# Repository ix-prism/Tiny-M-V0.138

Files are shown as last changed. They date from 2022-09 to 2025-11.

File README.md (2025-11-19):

# Tiny-M + Voron0.2 Mod
a mod for Voron0/Tiny-M 3D printer/一个基于Voron0/Tiny-M的3D打印机mod

This project is based on Tiny-M by Guido (gsl12).
Thanks for the great idea and all the work he put into it.

# 与 Tiny-M 的区别 / Differences from Tiny-M

- Voron 0.2 风格化外观  
  Stylized in the style of Voron 0.2

- 使用 MiniFrontBurner 打印头，支持 E3D V6 或 Bambu 热端  
  Uses the MiniFrontBurner toolhead, compatible with E3D V6 or Bambu hotends

- X 轴导轨更换为侧面安装的 MGN9H  
  X-axis linear rail replaced with a side-mounted MGN9H

- 挤出机更换为 Sherpa Mini  
  Extruder changed to Sherpa Mini

- 屏幕更换为 V0Display  
  Display replaced with V0Display

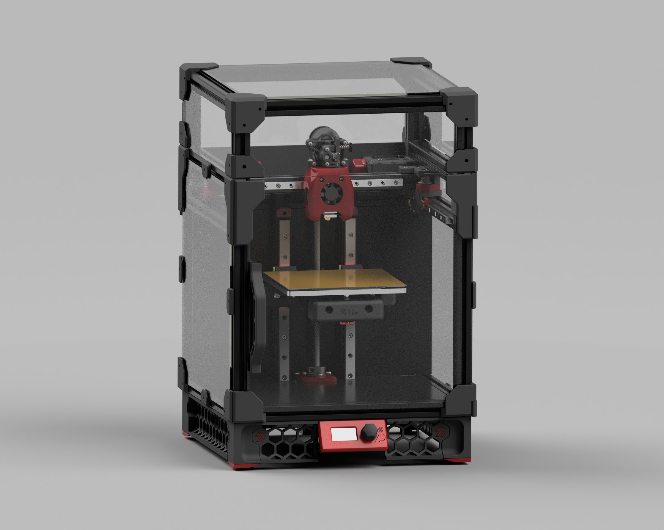
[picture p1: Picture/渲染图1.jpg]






)

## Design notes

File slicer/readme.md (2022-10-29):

切片配置文件建议套用Voron0.1或2.4的预设，并将平台大小改为150x150，高度150。

并更改打印机设置中的：

起始Gcode:

PrusaSlicer:

; M190 S0
; M109 S0 ; uncomment to remove set&wait temp gcode added automatically after this start gcode
print_start HOTEND=[first_layer_temperature[initial_tool]] BED=[first_layer_bed_temperature]

cura:

PRINT_START BED={material_bed_temperature_layer_0} HOTEND={material_print_temperature_layer_0}

SuperSlicer:

; M190 S0
; M109 S0 ; uncomment to remove set&wait temp gcode added automatically after this start gcode
print_start HOTEND={first_layer_temperature[initial_extruder] + extruder_temperature_offset[initial_extruder]} BED=[first_layer_bed_temperature] CHAMBER=[chamber_temperature]

结束Gcode:

print_end

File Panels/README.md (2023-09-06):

## Voron0.2样式封箱

### 黑色

Deck_Panel x1

Back_Panel x1

### 透明
门板 
270x294mm x1

侧板 
270x278mm x2

顶罩 
270x270mm x1

270x80mm  x5

厚度3mm

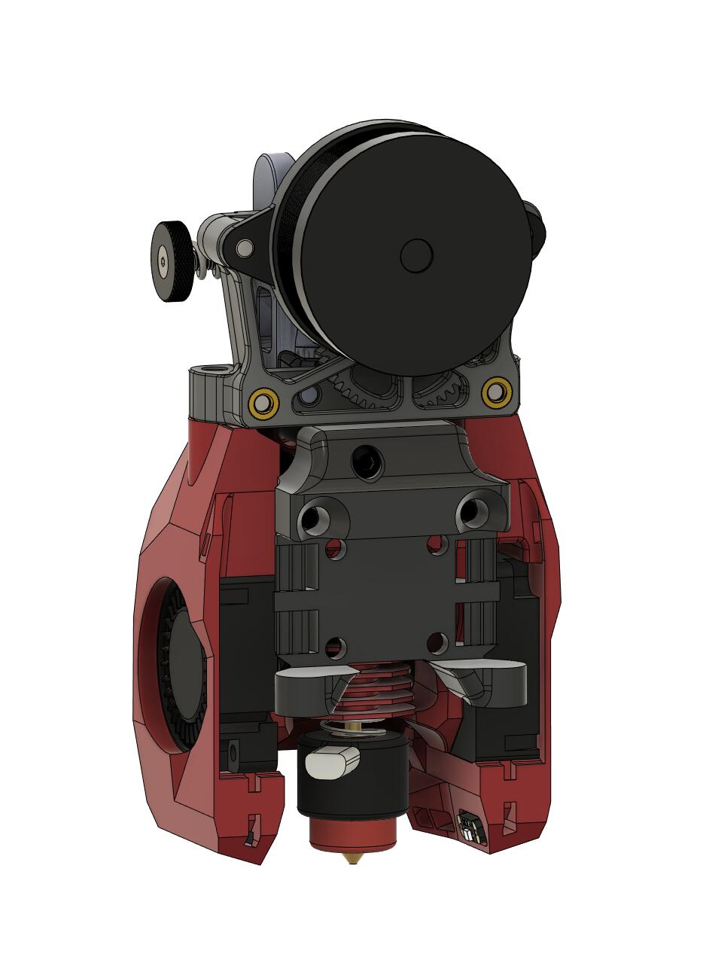
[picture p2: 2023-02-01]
Picture/Mini Stealthburner-Sherpa2.jpg

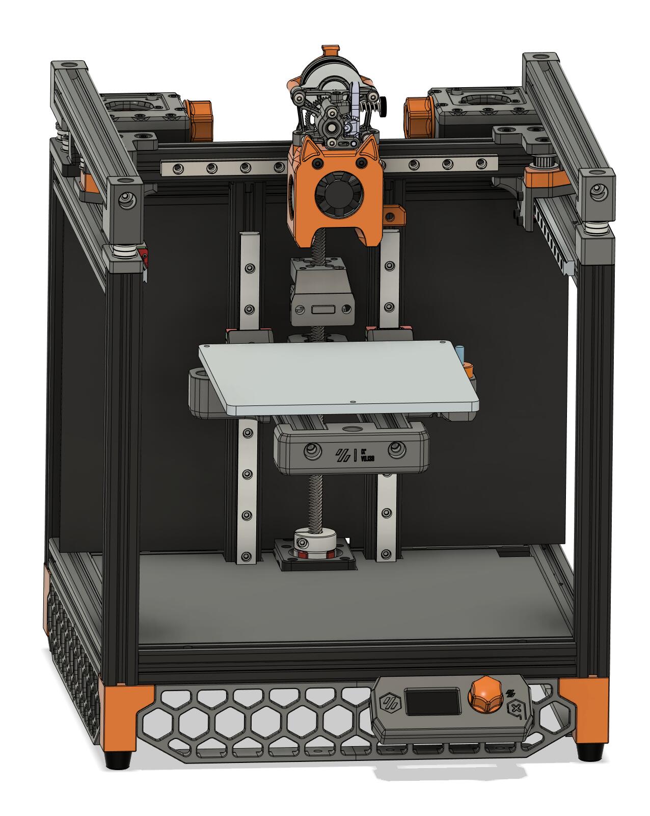
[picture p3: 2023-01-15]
Picture/rc2.jpg

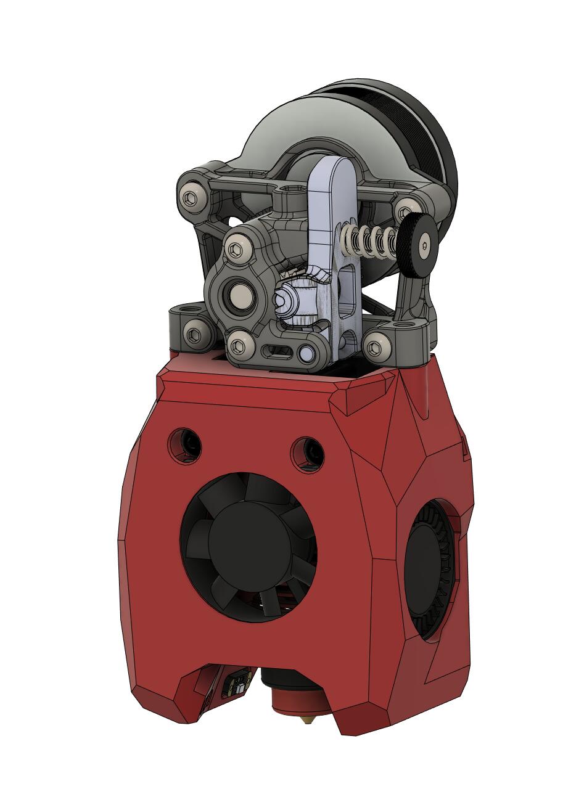
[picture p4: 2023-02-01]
Picture/Mini Stealthburner-Sherpa1.jpg

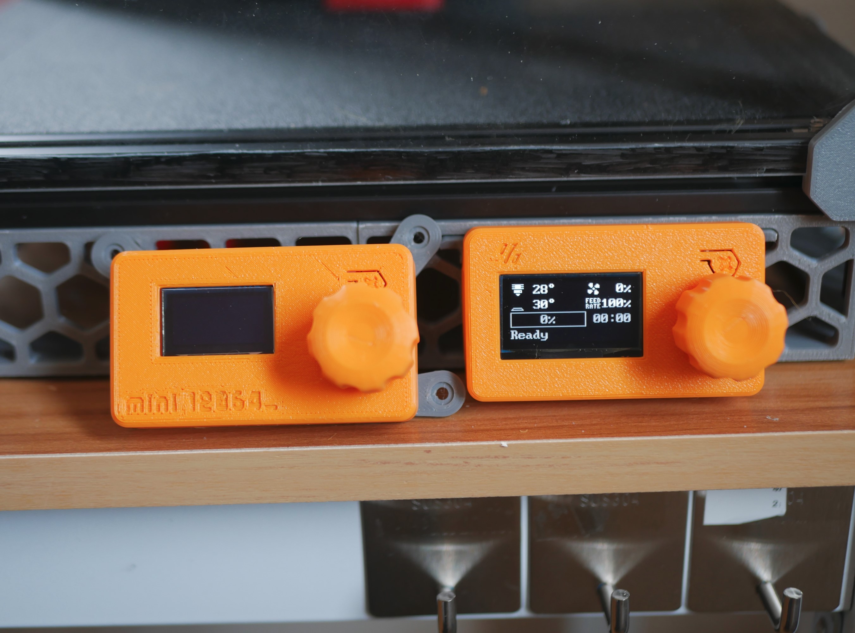
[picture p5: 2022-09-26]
Picture/实拍图1.jpg

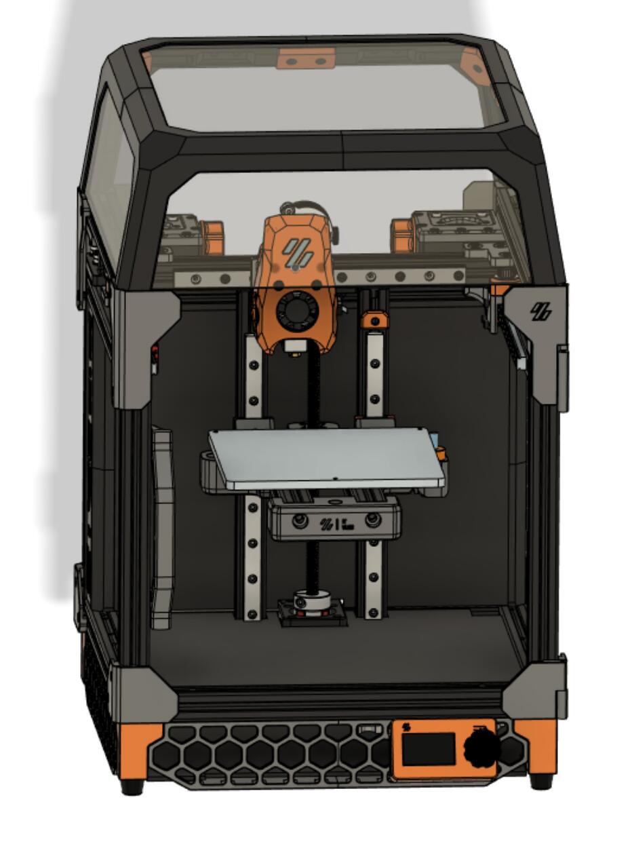
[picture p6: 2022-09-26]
Picture/picture.jpg

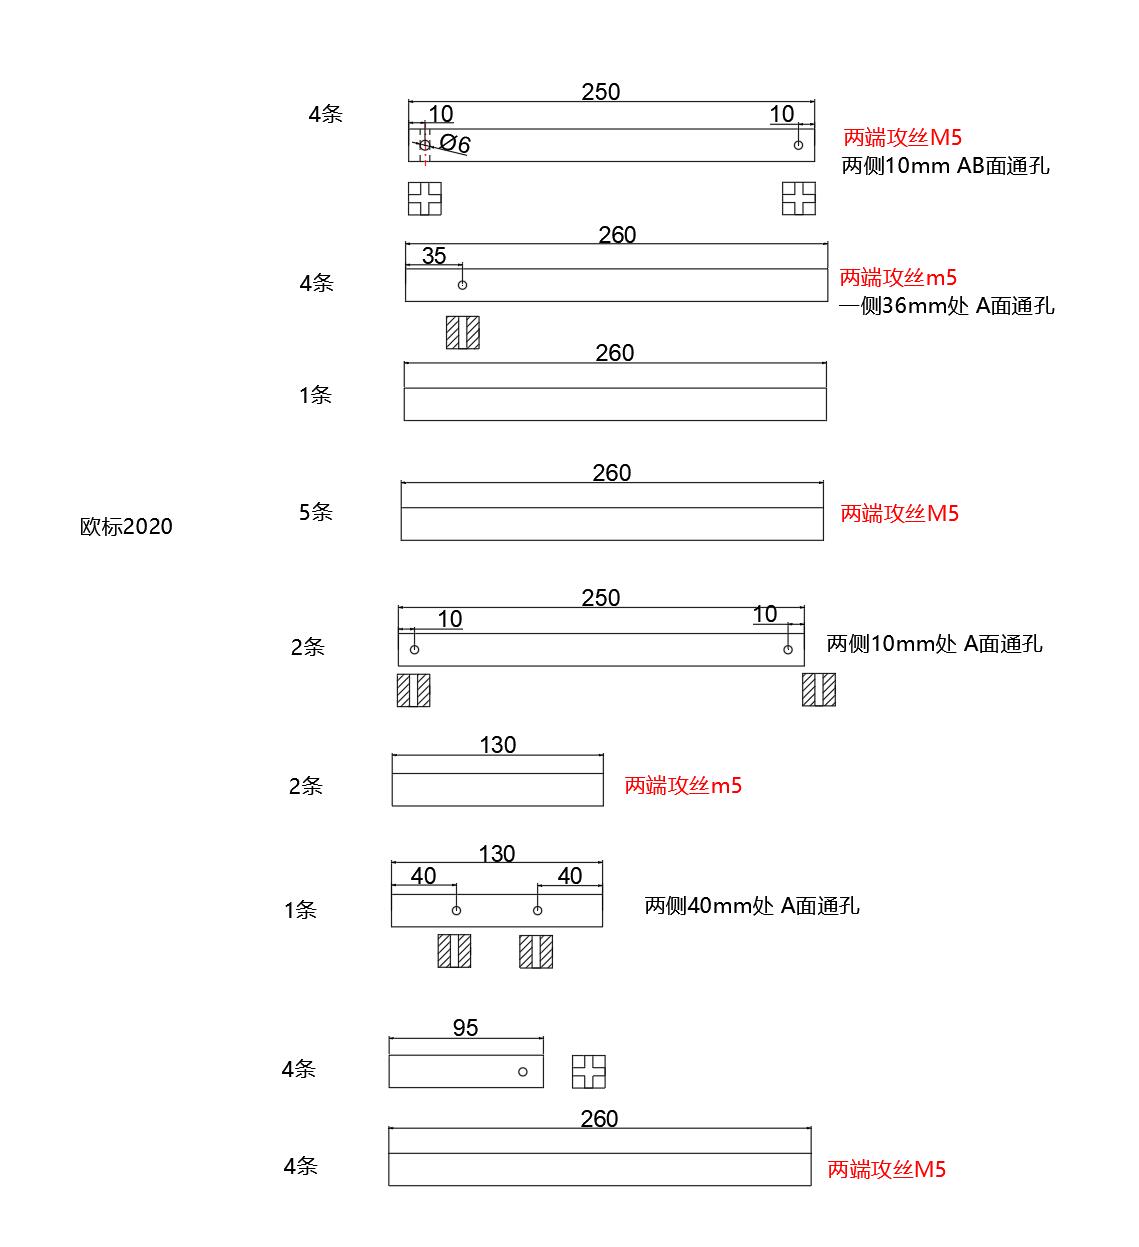
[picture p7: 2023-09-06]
frame/FRAME.jpg

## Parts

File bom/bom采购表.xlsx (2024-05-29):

 | 型号 | 数量 | 参考
紧固件 | m3x8 杯头 | 60 | https://detail.tmall.com/item.htm?abbucket=9&id=18273546578&ns=1&priceTId=213e391a17169841317497723e8a6d
 | m3x10 杯头 | 60 | https://detail.tmall.com/item.htm?abbucket=9&id=18273546578&ns=1&priceTId=213e391a17169841317497723e8a6d
 | m3x12 杯头 | 20 | https://detail.tmall.com/item.htm?abbucket=9&id=18273546578&ns=1&priceTId=213e391a17169841317497723e8a6d
 | m3x16 杯头 | 2 | https://detail.tmall.com/item.htm?abbucket=9&id=18273546578&ns=1&priceTId=213e391a17169841317497723e8a6d
 | m3x20 杯头 | 10 | https://detail.tmall.com/item.htm?abbucket=9&id=18273546578&ns=1&priceTId=213e391a17169841317497723e8a6d
 | m3x25 杯头 | 10 | https://detail.tmall.com/item.htm?abbucket=9&id=18273546578&ns=1&priceTId=213e391a17169841317497723e8a6d
 | m3x30 杯头 | 10 | https://detail.tmall.com/item.htm?abbucket=9&id=18273546578&ns=1&priceTId=213e391a17169841317497723e8a6d
 | m3x35 杯头 | 20 | https://detail.tmall.com/item.htm?abbucket=9&id=18273546578&ns=1&priceTId=213e391a17169841317497723e8a6d
 | m3x40 杯头 | 2 | https://detail.tmall.com/item.htm?abbucket=9&id=18273546578&ns=1&priceTId=213e391a17169841317497723e8a6d
 | m3x45 杯头 | 3 | https://detail.tmall.com/item.htm?abbucket=9&id=18273546578&ns=1&priceTId=213e391a17169841317497723e8a6d
 | m2x10自攻 | 20 | https://detail.tmall.com/item.htm?id=26788024998&rn=32485e43cd554b61808184f56eb92091&abbucket=6
 | m4x10杯头 | 4 | https://detail.tmall.com/item.htm?abbucket=9&id=18273546578&ns=1&priceTId=213e391a17169841317497723e8a6d
 | m5x8圆头 | 30 | https://detail.tmall.com/item.htm?id=35703239201&rn=ca5bd9221a8a0a63bc05ffa24d3150ff&abbucket=6
 | m5x10圆头 | 30 | https://detail.tmall.com/item.htm?id=35703239201&rn=ca5bd9221a8a0a63bc05ffa24d3150ff&abbucket=6
 | m5x16圆头 | 25 | https://detail.tmall.com/item.htm?id=35703239201&rn=ca5bd9221a8a0a63bc05ffa24d3150ff&abbucket=6
 | m5x30圆头 | 4 | https://detail.tmall.com/item.htm?id=35703239201&rn=ca5bd9221a8a0a63bc05ffa24d3150ff&abbucket=6
 | m5x35圆头 | 4 | https://detail.tmall.com/item.htm?id=35703239201&rn=ca5bd9221a8a0a63bc05ffa24d3150ff&abbucket=6
 | M5x40杯头 | 4 | https://detail.tmall.com/item.htm?abbucket=9&id=18273546578&ns=1&priceTId=213e391a17169841317497723e8a6d
 | M5x55圆头 | 4 | https://detail.tmall.com/item.htm?id=35703239201&rn=ca5bd9221a8a0a63bc05ffa24d3150ff&abbucket=6
 | 20型 M3弹珠螺母 | 30 | https://detail.tmall.com/item.htm?id=602648155862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
 | 20型 M5弹珠螺母 | 30 | https://detail.tmall.com/item.htm?id=602648155862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
 | M3六角螺母 | 4 | https://detail.tmall.com/item.htm?id=20955552239&rn=f7722f9d702b8c245503003701b63420&abbucket=6
 | M3 T螺母 | 70 | https://detail.tmall.com/item.htm?id=602648155862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
 | M5 T螺母 | 30 | https://detail.tmall.com/item.htm?id=602648155862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
 | 3x4x5土八热熔螺母 | 30 | https://detail.tmall.com/item.htm?priceTId=2147bfe017169844482451716efa16&id=654516657514&ns=1&abbucket=9
 | 5x6x7土八热熔螺母 |  | https://detail.tmall.com/item.htm?priceTId=2147bfe017169844482451716efa16&id=654516657514&ns=1&abbucket=9
 | 1x8x25黄色模具弹簧 | 3 | https://item.taobao.com/item.htm?priceTId=215040fc17169846375948829efd79&id=16269938500&ns=1&abbucket=9
传动件 | F695ZZ轴承 | 20 | https://item.taobao.com/item.htm?priceTId=215040fc17169846551052507efd79&id=650278182280&ns=1&abbucket=9
 | 5x8x1间隙垫片 | 20 | https://item.taobao.com/item.htm?priceTId=215040fc17169846849985018efd79&id=610328378642&ns=1&abbucket=9
 | T8丝杆导程8 210mm | 1 | https://item.taobao.com/item.htm?priceTId=215040fc17169847291951068efd79&id=559693268692&ns=1&abbucket=9
 | 联轴器 5x8mm | 1 | https://item.taobao.com/item.htm?priceTId=215040fc17169847469882688efd79&id=584297719001&ns=1&abbucket=9
 | 42步进电机（XY） |  | https://item.taobao.com/item.htm?priceTId=215040fc17169847953456946efd79&id=670665930208&ns=1&abbucket=9
 | 42步进电机（Z） | 3 | https://item.taobao.com/item.htm?priceTId=215040fc17169847607943979efd79&id=649664531631&ns=1&abbucket=9
 | 2GT同步轮 20齿 内孔5 | 3 | https://item.taobao.com/item.htm?priceTId=2147828b17169848125175875e9536&id=577469956078&ns=1&abbucket=9
 | 2GT惰轮20齿 内孔5 | 2 | https://item.taobao.com/item.htm?priceTId=2147828b17169848125175875e9536&id=559682437946&ns=1&abbucket=9
 | 35mm圆柱销 切槽（Voron2.4限位同款） | 1 | https://item.taobao.com/item.htm?priceTId=2147828b17169848327376922e9536&id=681231933442&ns=1&abbucket=9
 | mgn9h直线导轨 200mm | 3 | https://detail.tmall.com/item.htm?id=617754103685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
 | mgn12h直线导轨 200mm | 2
 | 2GT 6mm皮带 | 3 | https://item.taobao.com/item.htm?priceTId=2147828b17169848770261321e9536&id=719632885878&ns=1&abbucket=9
电子元件 | 微动开关 d2f 带弹片x2 不带弹片x1 | 3 | https://item.taobao.com/item.htm?priceTId=2147828b17169849159123369e9536&id=18868641543&ns=1&abbucket=9
 | 香橙派Zero 3 | 1 | https://detail.tmall.com/item.htm?priceTId=2147828b17169849839767753e9536&id=728078846964&ns=1&abbucket=9
 | 32GB TF卡 读卡器 | 1 | https://detail.tmall.com/item.htm?priceTId=2147828b17169849647936550e9536&id=659968673994&ns=1&abbucket=9
 | Bigtreetech SKR PICO | 1 | https://item.taobao.com/item.htm?priceTId=2147828b17169849432475100e9536&id=668879699263&ns=1&abbucket=9
 | 200W 24V开关电源 | 1 | https://detail.tmall.com/item.htm?id=546975228335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
 | C14电源插座 | 1 | https://item.taobao.com/item.htm?priceTId=2147822f17169850475763810efc68&id=652256774750&ns=1&abbucket=9
 | C13电源线 | 1 | https://item.taobao.com/item.htm?priceTId=2147820f17169850937438831e0b78&id=743432903716&ns=1&abbucket=9
 | 3010鼓风机 24V 15000rpm | 2 | https://item.taobao.com/item.htm?priceTId=2147820f17169851137411955e0b78&id=674712023015&ns=1&abbucket=9
 | 3010轴流风扇 24V 11000rpm | 1 | https://item.taobao.com/item.htm?spm=a1z10.3-c.w4002-22813209058.13.62e347bbOxIzJz&id=677180233734
 | V0Display OLED屏 | 1 | https://item.taobao.com/item.htm?priceTId=2147822717169851415963970e05de&id=710412503507&ns=1&abbucket=9
 | 18awg导线 | 1
 | 型号 | 数量
 | 风扇延长线 | 1
挤出机 | 拓竹热端 | 1 | https://item.taobao.com/item.htm?priceTId=2147822717169851780266019e05de&id=730602674552&ns=1&abbucket=9
 | 36圆饼步进电机 | 1 | https://item.taobao.com/item.htm?priceTId=2147822717169851924886664e05de&id=701941466920&ns=1&abbucket=9
 | BMG挤出机齿轮套件 | 1 | https://item.taobao.com/item.htm?spm=a1z10.3-c.w4002-24486160586.11.f24340daE31Nld&id=731773857096
 | 3x4mm铁氟龙管 | 1 | https://detail.tmall.com/item.htm?priceTId=2147826717169852219491882e4ea2&id=520837614528&ns=1&abbucket=9
 | 2x4mm铁氟龙管 | 1 | https://detail.tmall.com/item.htm?priceTId=2147826717169852219491882e4ea2&id=520837614528&ns=1&abbucket=9
杂项 | 橡胶脚垫 内孔5 | 4 | https://item.taobao.com/item.htm?priceTId=214781b217169852806426253eefb3&id=678365614319&ns=1&abbucket=9
 | 10X11 R18可开拖链 | 1 | https://item.taobao.com/item.htm?priceTId=214781b217169852939376897eefb3&id=676337595083&ns=1&abbucket=9
 | 尼龙理线网 | 1 | https://item.taobao.com/item.htm?priceTId=214782b617169853084064094edc52&id=23733868415&ns=1&abbucket=9
 | 尼龙扎带 | 10
 | 亚克力板 | 2
 | 理线槽15cm | 1 | https://click.simba.taobao.com/cc_im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
 | 3M双面胶 | 1
铝型材 | 250mm 两侧10mm通孔 攻丝 | 4
 | （四根立柱）
 | 260mm 一侧36mm通孔 攻丝 | 4
 | （Y左右线轨固定，线轨下方横梁）
 | 260mm 无其他处理 | 1
 | （X轴线轨）
 | 260mm 两端攻丝 | 5
 | （横梁）
 | 250mm 两端10mm通孔 | 2
 | （Z轴线轨）
 | 130mm 两端攻丝 | 1
 | （热床）
 | 130mm 两侧40mm通孔 | 2
 | （热床）
热床 | 150x150x6超平铝板 | 1
 | 120W 100x100加热垫 | 1
 | 150x150 PEI喷涂磁吸平台 | 1

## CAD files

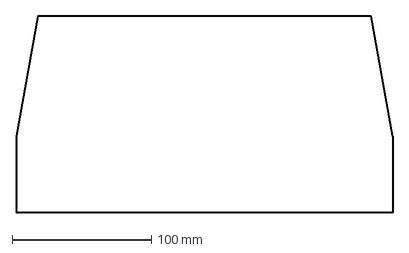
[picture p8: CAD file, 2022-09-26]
Panels/【透明】顶罩后.dxf
270.4 x 141.5 mm

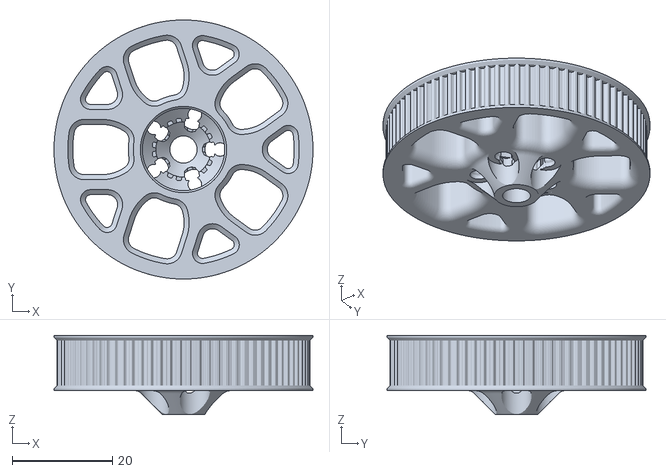
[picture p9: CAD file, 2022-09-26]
stls/Bed/belt_z/皮带z_80T.stl
51.6 x 51.6 x 15.8

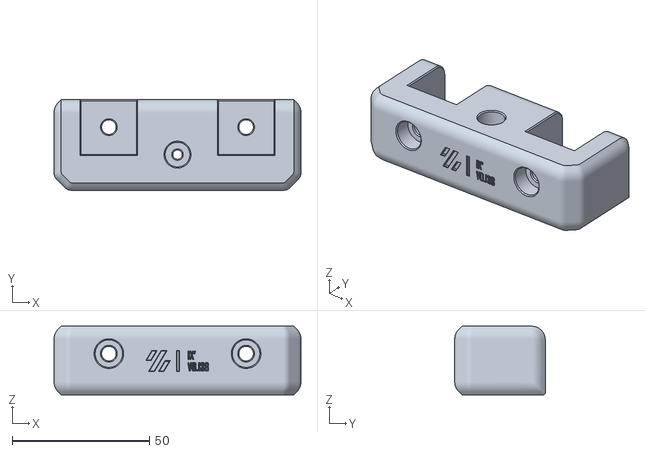
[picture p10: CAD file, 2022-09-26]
stls/Bed/带logo.stl
90.0 x 33.0 x 25.0

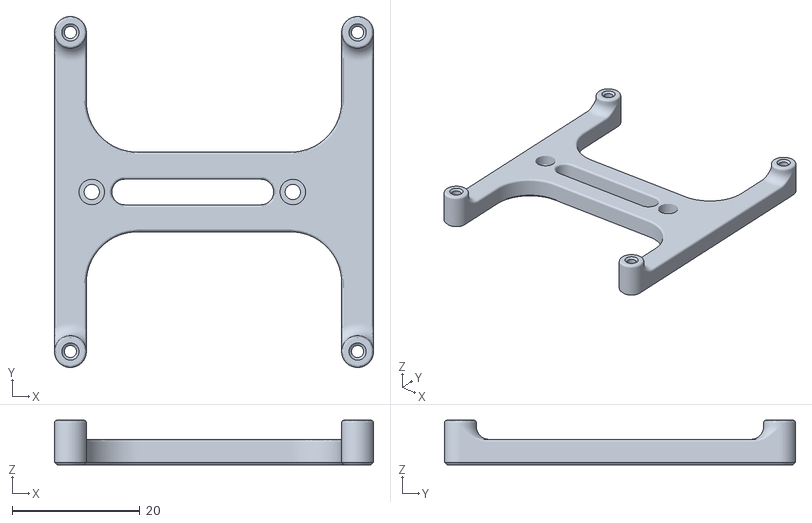
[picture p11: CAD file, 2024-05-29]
stls/Electronics/orangepi zero3 bracket.stl
50.0 x 55.0 x 7.00

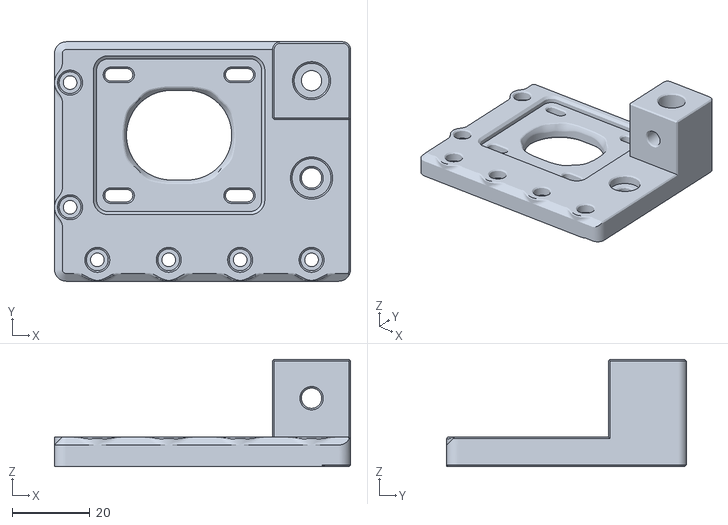
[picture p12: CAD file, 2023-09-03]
stls/Gantry/AB_drive_units/ab_drive v4 - b_drive_right_top_V4_V1.stl
76.0 x 61.5 x 27.6

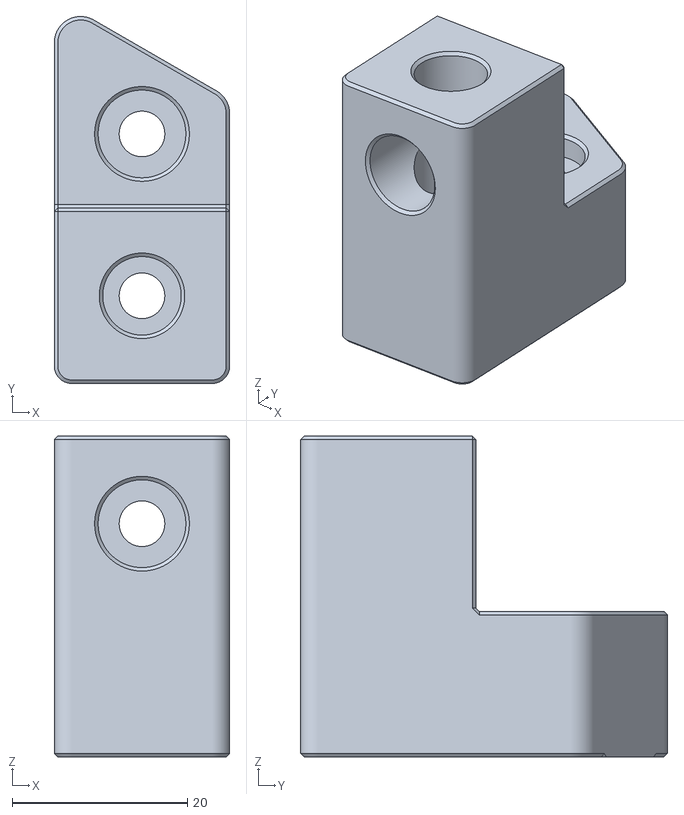
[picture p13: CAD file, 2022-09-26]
stls/Gantry/Front-Idler/front_idler_left_top_V4.stl
20.0 x 41.9 x 36.6

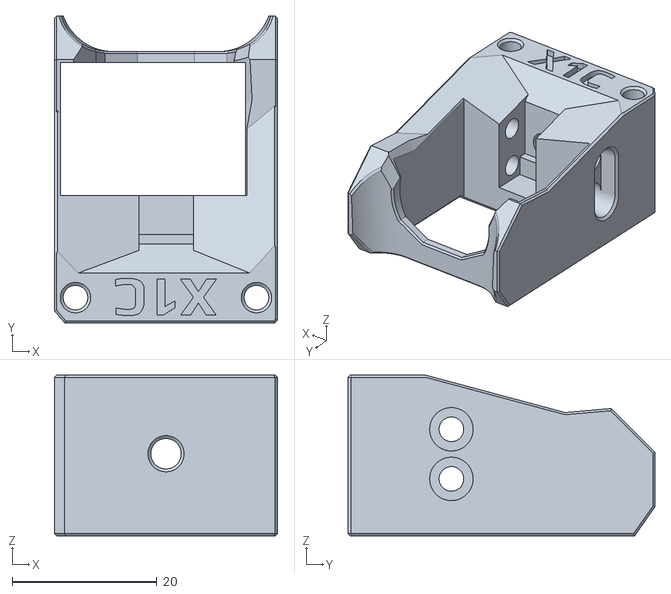
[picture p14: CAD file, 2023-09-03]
stls/Gantry/X_Axis/X_Carriage/[a]_FS_Hotend_Mount_Bambu_X1C.stl
30.8 x 42.4 x 22.2

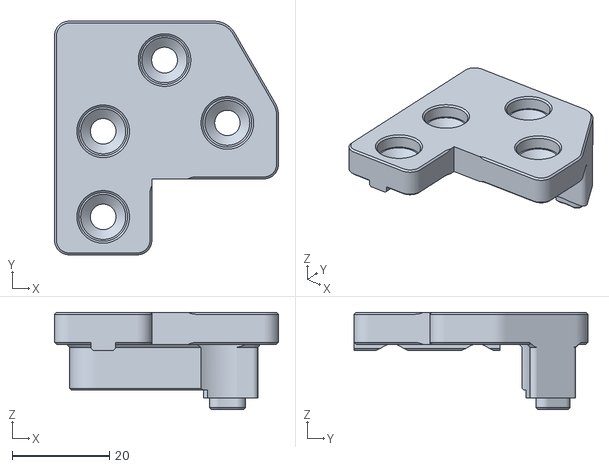
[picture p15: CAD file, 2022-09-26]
stls/Gantry/X_Axis/XY_Joint/右上.stl
46.0 x 48.0 x 20.0

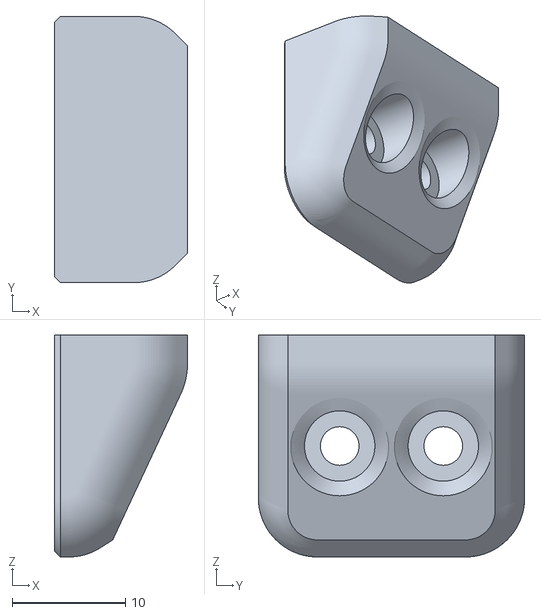
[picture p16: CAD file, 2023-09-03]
stls/Panel_Mounting-封箱/Door Latch x2.stl
11.7 x 23.5 x 19.6

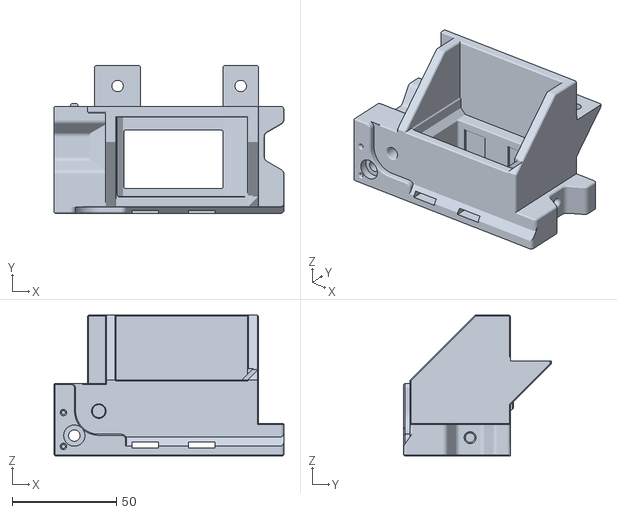
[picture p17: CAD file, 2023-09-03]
stls/skirts-裙边/Back_Left_Foot_V3.stl
110.4 x 70.8 x 67.6

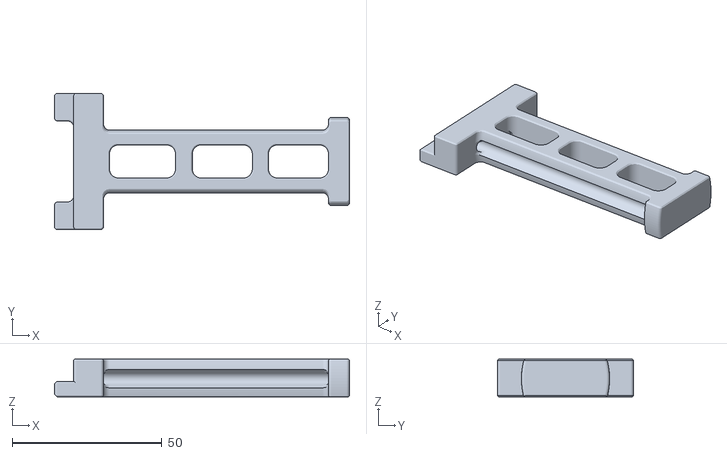
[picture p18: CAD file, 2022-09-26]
stls/Spool_Management/printed_parts - Spool Holder-5mm_mod.stl
98.4 x 45.4 x 12.5

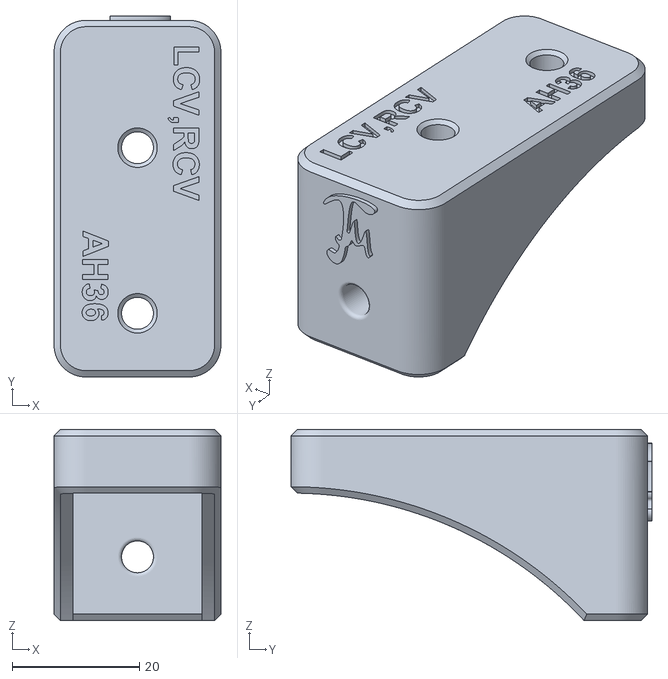
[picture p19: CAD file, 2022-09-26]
stls/Tools/Drill_Tap_Jig_B_.stl
26.2 x 56.7 x 30.0

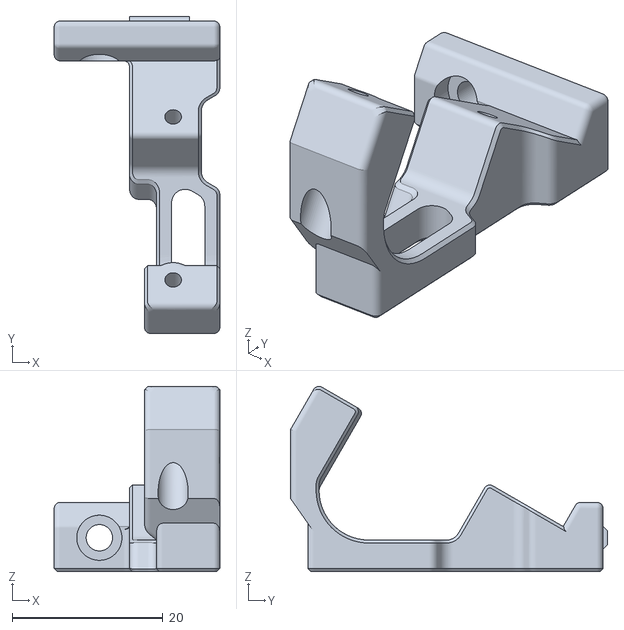
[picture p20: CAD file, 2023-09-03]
stls/V0Display-屏幕/Display_Mount_Right_x1.stl
22.0 x 42.1 x 24.6

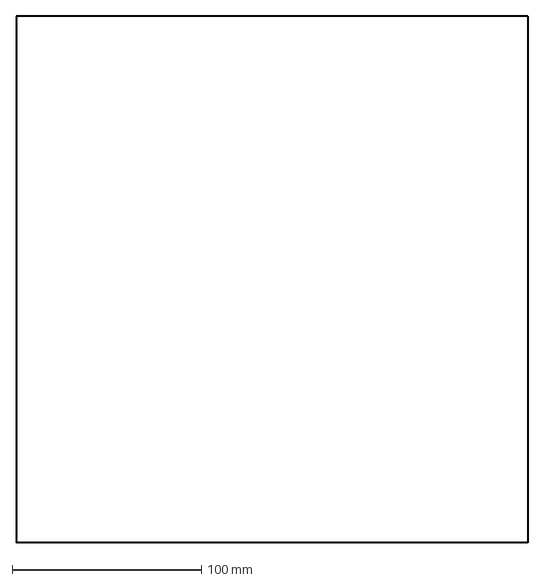
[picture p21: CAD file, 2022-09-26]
Panels/【透明2件】侧板左右.dxf
270.0 x 278.0 mm

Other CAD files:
stls/Bed/belt_z/皮带z_顶部导轮1.stl
stls/Bed/z_position_lower.stl
stls/Electronics/cam-摄像头固定.stl
stls/Gantry/AB_drive_units/ab_drive v4 - a_drive_left_top_V4_V1.stl
Panels/【皮带Z】【黑色】Back_Panel.dxf
Panels/【皮带Z】【黑色】Deck_Panel.dxf
Panels/【透明2件】顶罩左右.dxf
Panels/【透明】门板.dxf
Panels/【透明】顶罩上.dxf
Panels/【透明】顶罩前.dxf
Panels/【黑色】Back_Panel.dxf
Panels/【黑色】Deck_Panel.DXF
stls/Bed/[a]printed_parts - lead screw motor mount.stl
stls/Bed/belt_z/Motor bracket.stl
stls/Bed/belt_z/皮带z mf105.stl
stls/Bed/belt_z/皮带z mf85.stl
stls/Bed/belt_z/皮带z_固定皮带上.stl
stls/Bed/belt_z/皮带z_固定皮带下.stl
stls/Bed/belt_z/皮带z_固定皮带底.stl
stls/Bed/belt_z/皮带z_顶部导轮2.stl
stls/Bed/printed_parts - lead_skrew_nut_block_m4 (1).stl
stls/Bed/printed_parts - rear_bed_mount_left.stl
stls/Bed/z_positioner_upper.stl
stls/Electronics/4010风扇.stl
stls/Electronics/6010风扇.stl
stls/Electronics/Kitty A 四轴主板.stl
stls/Electronics/Orangepi_Zero3_mount.stl
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

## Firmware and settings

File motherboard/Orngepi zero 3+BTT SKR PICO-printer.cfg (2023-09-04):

[include mainsail.cfg]
[include v0display.cfg]
[include ./lcd_menu/lcd_menu.cfg]
[include timelapse.cfg]
# This file contains common pin mappings for the BIGTREETECH SKR Pico V1.0
# To use this config, the firmware should be compiled for the RP2040 with
# USB communication.

# The "make flash" command does not work on the SKR Pico V1.0. Instead,
# after running "make", copy the generated "out/klipper.uf2" file
# to the mass storage device in RP2040 boot mode

## Voron Design VORON 0.2 SKR Pico V1.0 config

## *** THINGS TO CHANGE/CHECK: ***
## MCU path                                                                     [mcu] section
## Z and Extruder motor currents                                                [tmc2209 stepper_*] sections. Uncomment the stepper motor you have
## Full steps per rotation for Extruder                                         [extruder] section
## Thermistor types                                                             [extruder] and [heater_bed] sections - See https://www.klipper3d.org/Config_Reference.html#common-thermistors for common thermistor types
## Motor currents                                                               [extruder] [stepper] and [_HOME_X/Y] macro sections
## PID tune                                                                     [extruder] and [heater_bed] sections
## Fine tune E steps                                                            [extruder] section
## For more info                                                                check https://docs.vorondesign.com/build/startup/#v0

[mcu]
#####################################################################
# Obtain definition by "ls -l /dev/serial/by-id/"
#####################################################################
#serial: /dev/serial/by-id/usb-Klipper_rp2040_REPLACE_WITH_YOUR_VALUE
serial: /dev/ttyS5 											# for UART connection
restart_method: command

######################################################################
# 共振补偿
######################################################################

[mcu opi]
serial: /tmp/klipper_host_mcu

[adxl345]
cs_pin: opi:gpio72
spi_bus: spidev1.0

[resonance_tester]
accel_chip: adxl345
probe_points:
    75,75,20 # 更改为热床中心点，依次为x,y,z

###################################################################
## 打印机限制
###################################################################

[printer]
kinematics: corexy
max_velocity: 500
max_accel: 8000
max_z_velocity: 15
max_z_accel: 300
square_corner_velocity: 6.0

#####################################################################
#      X/Y 电机设置
#####################################################################

[stepper_x]
step_pin: gpio11
## Refer to https://docs.vorondesign.com/build/startup/#v0
dir_pin: gpio10                                                     # [需调整]检查电机运动方向，如果反了，在gpio10前面增加一个!，如果已存在就移除!
enable_pin: !gpio12
rotation_distance: 40
microsteps: 32
full_steps_per_rotation: 200                                        # 0.9度电机设置为400，1.8度电机设置为200
endstop_pin: ^gpio4
position_endstop: 155
position_max: 155
homing_speed: 60                                                    # for sensorless homing it is recommended not to go above 40mm/s   
homing_retract_dist: 0
homing_positive_dir: true

[tmc2209 stepper_x]
uart_pin: gpio9
tx_pin: gpio8
uart_address: 0
interpolate: False
run_current: 1.1           
# you need to calculate the run_current value using the equation (rated_motor_current * 0.707 = Maximum_run_current) start with a value that is about 60%-70% of your maximum value.
sense_resistor: 0.110
stealthchop_threshold: 0                                            # 设为 999999 开启stealthchop（静音）模式, 0为spreadcycle（高速）模式
#diag_pin: ^gpio4    												# 你需要插上无限位回零跳线帽来使它工作
#driver_SGTHRS: 255  												# [需调整]设置255为无限位回零最大灵敏度，0为最低灵敏度

[stepper_y]
step_pin: gpio6
## Refer to https://docs.vorondesign.com/build/startup/#v0
dir_pin: gpio5                                                      # [需调整]检查电机运动方向，如果反了，在gpio5前面增加一个!，如果已存在就移除!
enable_pin: !gpio7
rotation_distance: 40
microsteps: 32
full_steps_per_rotation: 200                                        # 0.9度电机设置为400，1.8度电机设置为200
endstop_pin: ^gpio3
position_endstop: 150
position_max: 150
homing_speed: 60                                                    # for sensorless homing it is recommended not to go above 40mm/s   
homing_retract_dist: 0
homing_positive_dir: true

[tmc2209 stepper_y]
uart_pin: gpio9
tx_pin: gpio8
uart_address: 2
interpolate: False
run_current: 1.1            
# you need to calculate the run_current value using the equation (rated_motor_current * 0.707 = Maximum_run_current) start with a value that is about 60%-70% of your maximum value.
sense_resistor: 0.110
stealthchop_threshold: 0                                            # 设为 999999 开启stealthchop（静音）模式, 0为spreadcycle（高速）模式
diag_pin: ^gpio3    												# 你需要插上无限位回零跳线帽来使它工作
driver_SGTHRS: 255  												# [需调整]设置255为无限位回零最大灵敏度，0为最低灵敏度

#####################################################################
#   Z 电机设置
#####################################################################

[stepper_z]
step_pin: gpio19
dir_pin: !gpio28                                                    # [需调整]检查电机运动方向，如果反了，在gpio10前面增加一个!，如果已存在就移除!
enable_pin: !gpio2
rotation_distance: 8                                                # For T8x8 integrated lead screw
microsteps: 32
endstop_pin: ^gpio25
position_endstop: 0
position_max: 150
position_min: -1.5
homing_speed: 20
second_homing_speed: 3.0
homing_retract_dist: 3.0


[tmc2209 stepper_z]
uart_pin: gpio9
tx_pin: gpio8
uart_address: 1
interpolate: False
## For OMC (StepperOnline) 17LS13-0404E-200G 0.4A 
run_current: 0.4
## For LDO-42STH25-1004CL200E 1.0A
#run_current: 0.37
sense_resistor: 0.110
stealthchop_threshold: 0                                            # Set to 999999 to turn stealthchop on, and 0 to use spreadcycle

#####################################################################
#   挤出机
#####################################################################

[extruder]
step_pin: gpio14
dir_pin: gpio13                                                     # [需调整]检查电机运动方向，如果反了，在gpio13前面增加一个!，如果已存在就移除!
enable_pin: !gpio15
full_steps_per_rotation: 400                                       # Set to 200 for LDO 1.8° stepper motor, and set to 400 for OMC(StepperOnline) 0.9° stepper motor
rotation_distance: 23.5                                            # See calibrating rotation_distance on extruders doc
gear_ratio: 50:16                                                   # For Mini Afterburner
microsteps: 32
nozzle_diameter: 0.400
filament_diameter: 1.750
heater_pin: gpio23
## Check what thermistor type you have. See https://www.klipper3d.org/Config_Reference.html#common-thermistors for common thermistor types.
## Use "Generic 3950" for NTC 100k 3950 thermistors
sensor_type: Generic 3950
sensor_pin: gpio27
control: pid                                                        # Do PID calibration after initial checks
pid_Kp: 28.182
pid_Ki: 1.978
pid_Kd: 100.397
min_temp: -100
max_temp: 320
min_extrude_temp: 170
max_extrude_only_distance: 150
max_extrude_cross_section: 0.8
pressure_advance: 0.02                                               # See tuning pressure advance doc
pressure_advance_smooth_time: 0.040

[tmc2209 extruder]
uart_pin: gpio9
tx_pin: gpio8
uart_address: 3
interpolate: False
## For OMC (StepperOnline) 14HR07-1004VRN 1A 0.9°
run_current: 0.5 # for OMC 14HR07-1004VRN rated at 1A
## For LDO LDO 36STH17-1004AHG 1A 1.8° 
#run_current: 0.3 # for LDO 36STH17-1004AHG
## For LDO LDO 36STH20-1004AHG 1A 1.8° 
#run_current: 0.6 # for LDO 36STH20-1004AHG
sense_resistor: 0.110
stealthchop_threshold: 0                                            # Set to 0 for spreadcycle, avoid using stealthchop on extruder

#####################################################################
#   热床加热
#####################################################################

[heater_bed]
heater_pin: gpio21
## Check what thermistor type you have. See https://www.klipper3d.org/Config_Reference.html#common-thermistors for common thermistor types.
## Use "Generic 3950" for Keenovo heaters
sensor_type: Generic 3950
sensor_pin: gpio26
smooth_time: 3.0
#max_power: 0.6                                                     # Only needed for 100w pads
min_temp: -100
max_temp: 120
control: pid                                                        # Do PID calibration after initial checks
pid_kp: 68.453
pid_ki: 10.800
pid_kd: 107.163

#####################################################################
# 风扇控制
#####################################################################

[heater_fan hotend_fan]
pin: gpio18
max_power: 1.0
kick_start_time: 0.5
heater: extruder
heater_temp: 50.0
#fan_speed: 1.0                                                     # You can't PWM the delta fan unless using blue wire
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

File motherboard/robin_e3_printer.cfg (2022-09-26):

# MKS Robin E3

[stepper_x]
step_pin: PC0
dir_pin: PB2
enable_pin: !PC13
microsteps: 16
rotation_distance: 40
endstop_pin: ^PA12 #tmc2209_stepper_x:virtual_endstop
position_endstop: 155
position_max: 155
homing_speed: 30
homing_retract_dist: 0

[stepper_y]
step_pin: PC2
dir_pin: PB9
enable_pin: !PB12
microsteps: 16
rotation_distance: 40
endstop_pin: ^PA11  #tmc2209_stepper_y:virtual_endstop
position_endstop: 150
position_max: 150
homing_speed: 30
homing_retract_dist: 0

[stepper_z]
step_pin: PC14
dir_pin: PC15
enable_pin: !PB8
microsteps: 16
rotation_distance: 4
endstop_pin: ^PC6
position_endstop: 0
position_min: -1
position_max: 150
homing_speed: 5

[extruder]
step_pin: PB4
dir_pin: PB3
enable_pin: !PB5
microsteps: 16
rotation_distance: 22.7
gear_ratio: 50:10
full_steps_per_rotation: 200	#200 for 1.8 degree, 400 for 0.9 degree
nozzle_diameter: 0.400
filament_diameter: 1.750
pressure_advance: 0.05
pressure_advance_smooth_time: 0.040
heater_pin: PC9
sensor_type: NTC 100K MGB18-104F39050L32
sensor_pin: PA0
#control: pid
#pid_Kp: 19.719
#pid_Ki: 0.9
#pid_Kd: 80
min_temp: 0
max_temp: 320

[thermistor NTC 10K]
temperature1: 25
resistance1: 10000
temperature2: 40
resistance2: 5315
temperature3: 65
resistance3: 2067

[heater_bed]
heater_pin: PC8
sensor_type: NTC 10K
sensor_pin: PA1
min_temp: 0
max_temp: 120
control: pid
pid_Kp: 57.140
pid_Ki: 3.256
pid_Kd: 250.704

[idle_timeout]
timeout: 3600

[tmc2209 stepper_x]
uart_pin: PC7
run_current: 1.5
#hold_current: 0.500
stealthchop_threshold: 0
interpolate: True
sense_resistor: 0.110
#diag_pin: ^PA12      # Set to MCU pin connected to TMC DIAG pin
#driver_SGTHRS: 65   # 255 is most sensitive value, 0 is least sensitiv      # Set to MCU pin connected to TMC DIAG pin

[tmc2209 stepper_y]
uart_pin: PD2
run_current: 1.5
#hold_current: 0.500
stealthchop_threshold: 0
interpolate: true
sense_resistor: 0.110
#diag_pin: ^PA11      # Set to MCU pin connected to TMC DIAG pin
#driver_SGTHRS: 100   # 255 is most sensitive value, 0 is least sensitiv      # Set to MCU pin connected to TMC DIAG pin

[tmc2209 stepper_z]
uart_pin: PC12
run_current: 0.8
#hold_current: 0.3
stealthchop_threshold: 0
interpolate: true


[tmc2209 extruder]
uart_pin: PC11
run_current: 0.5
stealthchop_threshold: 999999
interpolate: true

[fan]
pin: PA8

#[bltouch]
#sensor_pin: ^PC6
#control_pin: PA3
#...

[mcu]
serial: /dev/serial/by-id/usb-1a86_USB_Serial-if00-port0
restart_method: command

[temperature_sensor raspberry_pi]
sensor_type: temperature_host
min_temp: 10
max_temp: 100

[printer]
kinematics: corexy
max_velocity: 300
max_accel: 5000
square_corner_velocity: 20
max_z_velocity: 5
max_z_accel: 50

# EXP1 / EXP2 (display) pins
[board_pins]
aliases:
    # EXP1 header
    EXP1_1=PC1, EXP1_3=PA4, EXP1_5=PA6, EXP1_7=PC4, EXP1_9=<GND>,
    EXP1_2=PC3, EXP1_4=PA5, EXP1_6=PA7, EXP1_8=PC5, EXP1_10=<5V>,
    # EXP2 header
    EXP2_1=PB14, EXP2_3=PB11, EXP2_5=PB0,  EXP2_7=PC10,  EXP2_9=<GND>,
    EXP2_2=PB13, EXP2_4=PA15, EXP2_6=PB15, EXP2_8=<RST>, EXP2_10=<NC>

[virtual_sdcard]
path: ~/gcode_files

[pause_resume]

[gcode_macro PRINT_START]
gcode:
  G90
  {% set bedtemp = params.BED|int %} #设置热床温度
  {% set hotendtemp = params.HOTEND|int %} #打印头温度
  M190 S{bedtemp}
  M109 S{hotendtemp}
  #画线
  G28
  G92 E0; #重置挤出
  G90 #设置绝对坐标系
  G0 X0 Y5 F6000
  G0 Z0.35
  G91 #设置坐标体系为相对坐标
  G1 Y120 E20 F1200
  G0 z5 #抬高z轴5mm
  G92 E0; #重置挤出
  G90 #设置绝对坐标体系

[gcode_macro PRINT_END]
gcode:
  M104 S0 #停止加热
  M140 S0
  G91 #设置相对坐标系
  G1 E-5 F800 #回抽5mm
  G28 X0 Y0  #X轴回零
  #M84     #关闭电机


[gcode_macro CANCEL_PRINT]
description: Cancel the actual running print
rename_existing: CANCEL_PRINT_BASE
gcode:
  G91 #相对坐标
  G1 E-5 F800
  G28 X0
  M84
  TURN_OFF_HEATERS
  CANCEL_PRINT_BASE


[display_status]

#[bltouch]
#sensor_pin: ^PD2
#control_pin:PB5
#x_offset: -44
#y_offset: -14
#z_offset: 3.099
#speed: 10.0
#samples: 2
#samples_result: median
#sample_retract_dist: 3.0
#samples_tolerance: 0.1
#samples_tolerance_retries: 1

[safe_z_home]
home_xy_position: 151,142 # Change coordinates to the center of your print bed
speed: 5
z_hop: 10                 # Move up 10mm
z_hop_speed: 5

  
[gcode_macro G29]
gcode:
  BED_MESH_CLEAR
  G28
  BED_MESH_CALIBRATE
  BED_MESH_PROFILE SAVE=name
  SAVE_CONFIG
  BED_MESH_PROFILE LOAD=name


######################################################################
# mini12864 1.3
######################################################################
 
[display]
lcd_type: sh1106
cs_pin: EXP1_4
dc_pin: EXP1_6
reset_pin: EXP1_7
contrast: 255
vcomh: 0
invert: False
x_offset: 2
encoder_pins: ^EXP2_3, ^EXP2_5
click_pin: ^!EXP1_2
## Some micro-controller boards may require an spi bus to be specified:
#spi_bus: spi
## Alternatively, some micro-controller boards may work with software spi:
spi_software_miso_pin: EXP1_8
spi_software_mosi_pin: EXP1_3
spi_software_sclk_pin: EXP1_5
 
[output_pin beeper]
pin: EXP1_1

#*# <---------------------- SAVE_CONFIG ---------------------->
#*# DO NOT EDIT THIS BLOCK OR BELOW. The contents are auto-generated.
#*#
#*# [extruder]
#*# control = pid
#*# pid_kp = 14.716
#*# pid_ki = 1.044
#*# pid_kd = 51.874
